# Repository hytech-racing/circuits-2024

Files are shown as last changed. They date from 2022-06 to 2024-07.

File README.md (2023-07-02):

HyTech Logo

# 2024 Circuits

Repository for all of the circuits for the 2023-2024 car.

## Getting Started with this Git Repository
1. Follow HyTech's [Software Guide](https://github.com/hytech-racing/training/tree/master/Resources).
2. Create a GitHub account if you don't already have one.
3. Download and install [GitHub Desktop](https://desktop.github.com/) (basic) or [Git CLI](https://git-scm.com/book/en/v2/Getting-Started-Installing-Git) (advanced).
    * If you are using GitHub Desktop for the first time, be sure to read the [User Guide](https://help.github.com/desktop/guides/).
    * If you are using Git for the first time, you should start off by reading a tutorial. There are many available online:
        * [Pro Git book](https://git-scm.com/book/en/v2)
        * [Atlassian Git Tutorial](https://www.atlassian.com/git/tutorials/)
    * You may want to keep a copy of [GitHub's Git Cheat Sheet](https://services.github.com/kit/downloads/github-git-cheat-sheet.pdf) as a reference.
4. Talk to your subteam lead to be added to the team within the GitHub organization.
5. Clone this repository to your computer using the URLs:
    * SSH: `git@github.com:hytech-racing/circuits-2024.git`
    * HTTPS: `https://github.com/hytech-racing/circuits-2024.git`

## Getting Started with EAGLE
1. Follow HyTech's [Software Guide](https://github.com/hytech-racing/training/tree/master/Resources).
2. Download and install [EAGLE](https://www.autodesk.com/products/eagle/overview)
3. Get the free [Educational License](https://www.autodesk.com/education/free-software/eagle) (a .edu email address is required)

## Github Software Guidelines and Electrical Designs Rules Review Process
Follow HyTech's [Github Software Guidelines](https://gtvault.sharepoint.com/:w:/r/sites/HyTechRacing2/Shared%20Documents/Electrical%20-%20All/HT06/Guidelines%20Rules%20and%20Procedures/Github%20Software%20Guide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) to understand our development flow and pull request procedure.
Follow HyTech's [Electrical Designs Rules Review Process](https://gtvault.sharepoint.com/:w:/r/sites/HyTechRacing2/Shared%20Documents/Electrical%20-%20All/HT06/Guidelines%20Rules%20and%20Procedures/Electrical%20Designs%20Ru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) to understand circuit design flow. 

## Circuit Board Versioning Scheme
* New boards must start their numbering at revision 1.
* Revision numbers must be incremented by 1 when a physical board is manufactured, but not at any other time.
* After a board is manufactured, the files corresponding to the manufactured version should not be modified.
* Circuit boards based off of a previous year's design should increment based off of the previous board's revision number.

## More Information
* [Software Guide](https://github.com/hytech-racing/training/tree/master/Resources)
* [Team Site](https://hytechracing.gatech.edu/)
* [Facebook](https://www.facebook.com/HyTechRacing/)
* [Engage](https://gatech.campuslabs.com/engage/organization/hytech-racing)

## License
This project is licensed under the GPL License v3.0. See the [LICENSE](LICENSE) file for more information.

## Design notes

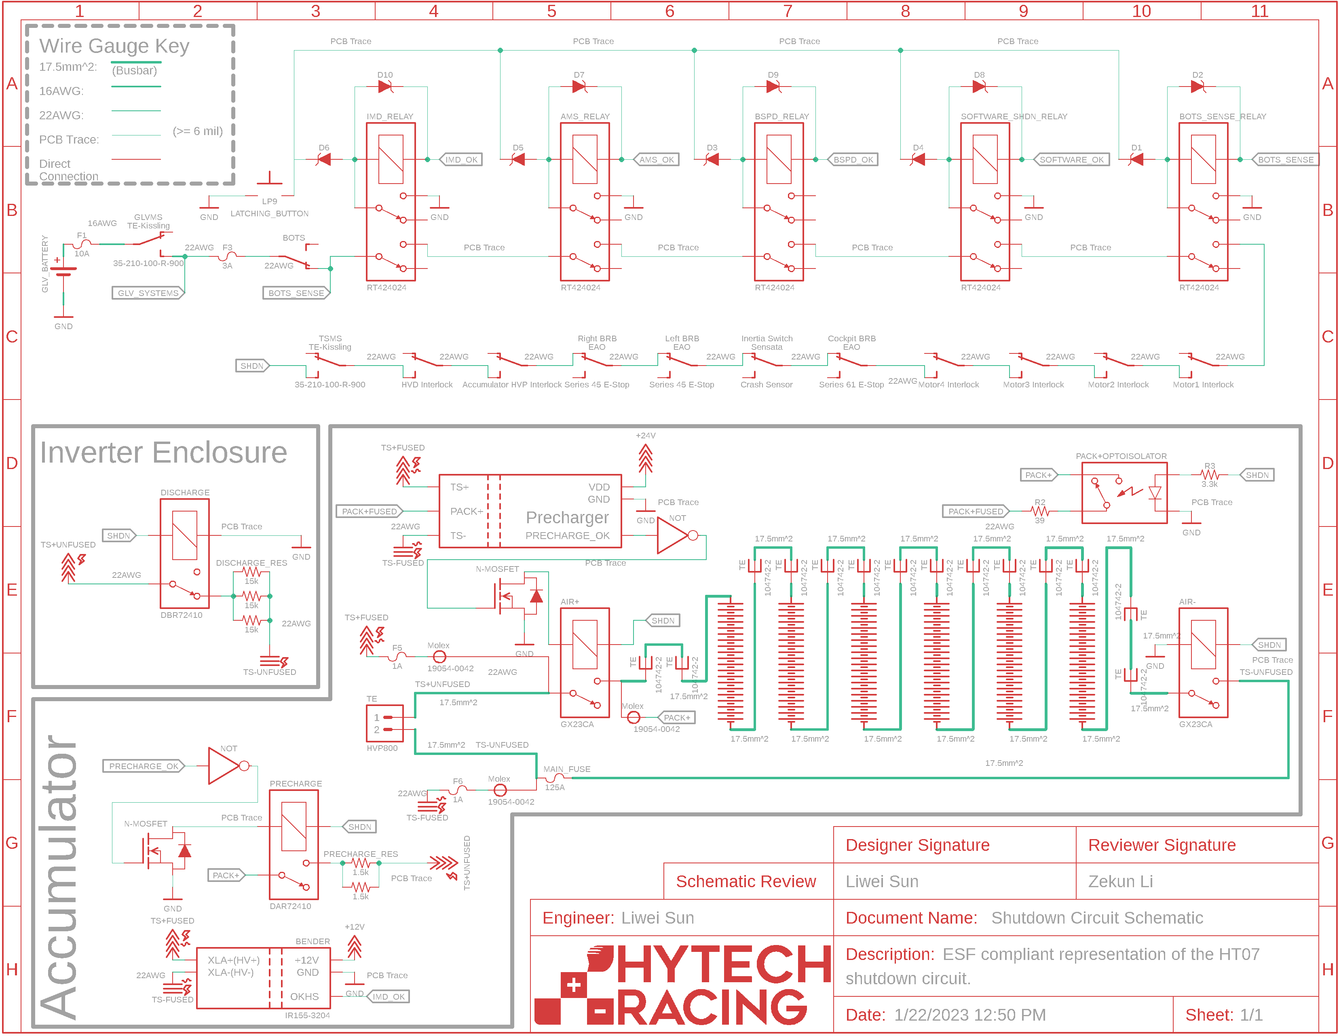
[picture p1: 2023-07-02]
ESF Schematics/2023/Shutdown Circuit Schematic.png

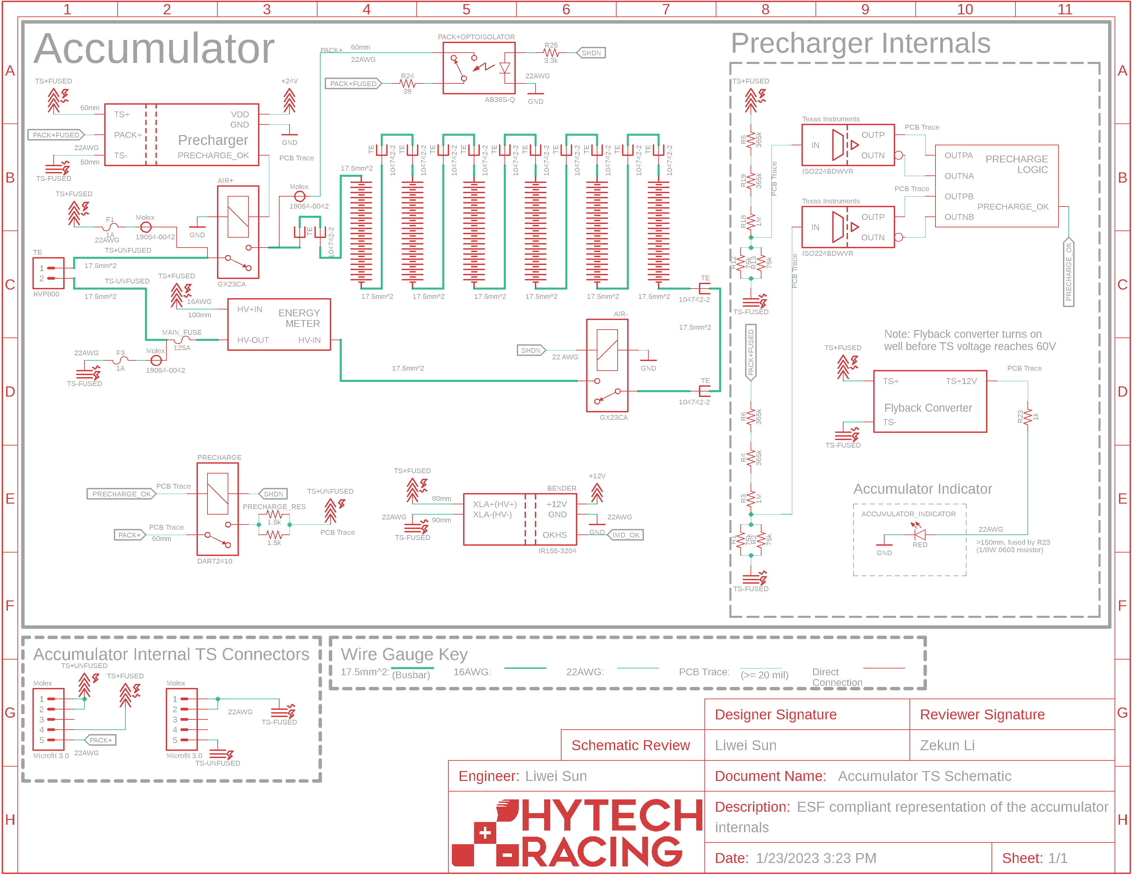
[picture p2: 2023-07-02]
ESF Schematics/2023/Accumulator TS Schematic.png

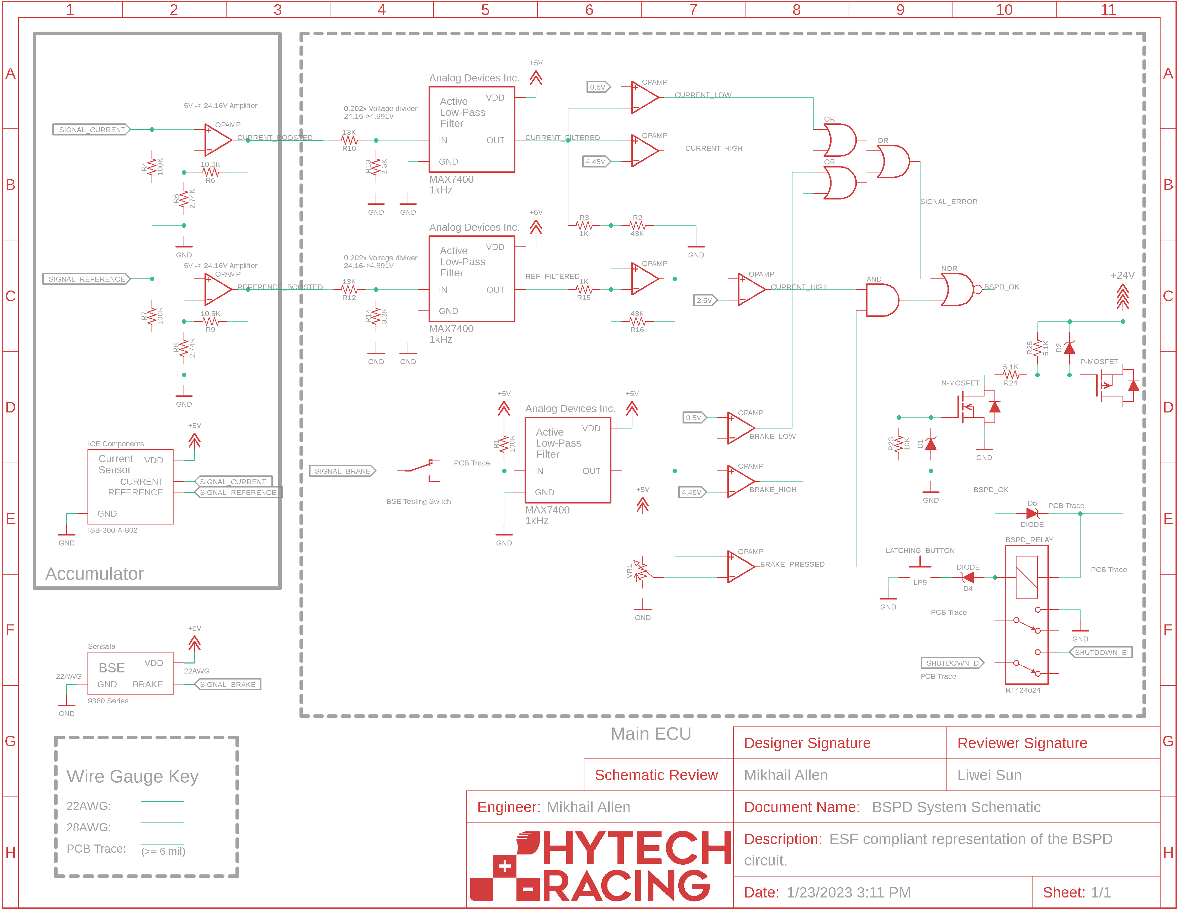
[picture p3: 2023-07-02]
ESF Schematics/2023/BSPD System Schematic.png

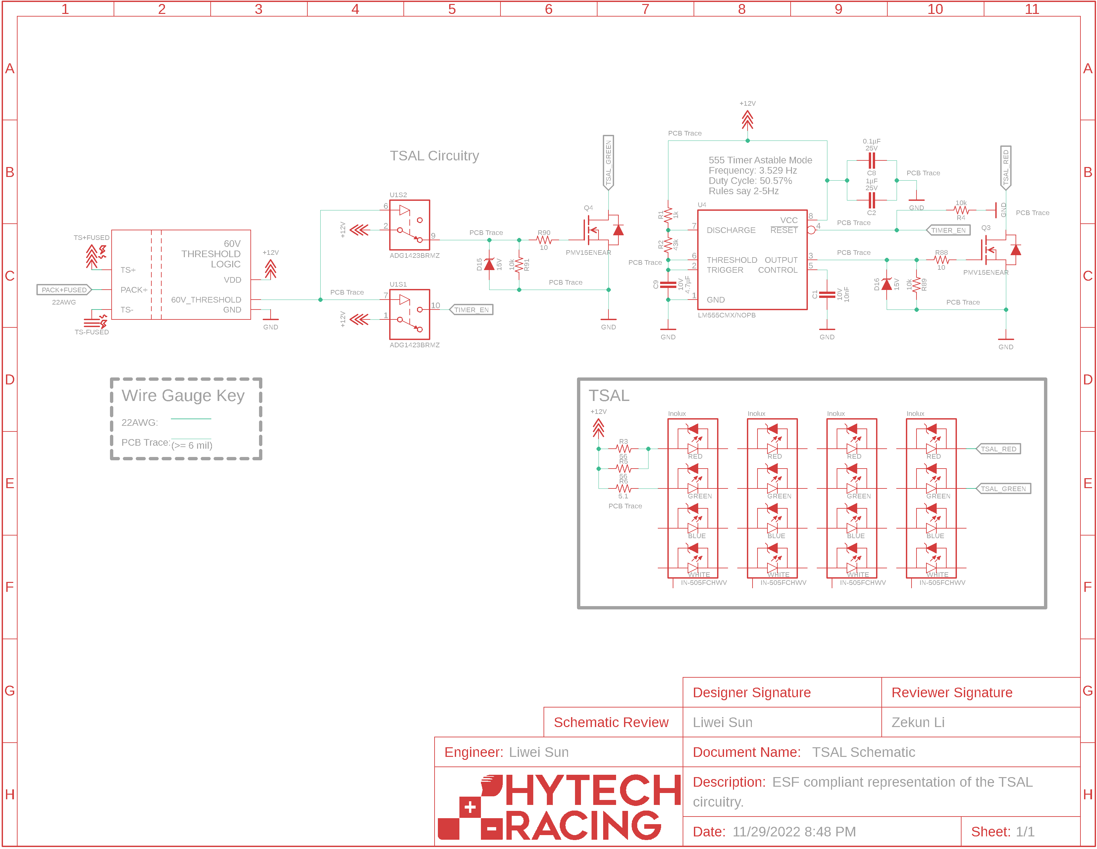
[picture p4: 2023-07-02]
ESF Schematics/2023/TSAL Schematic.png

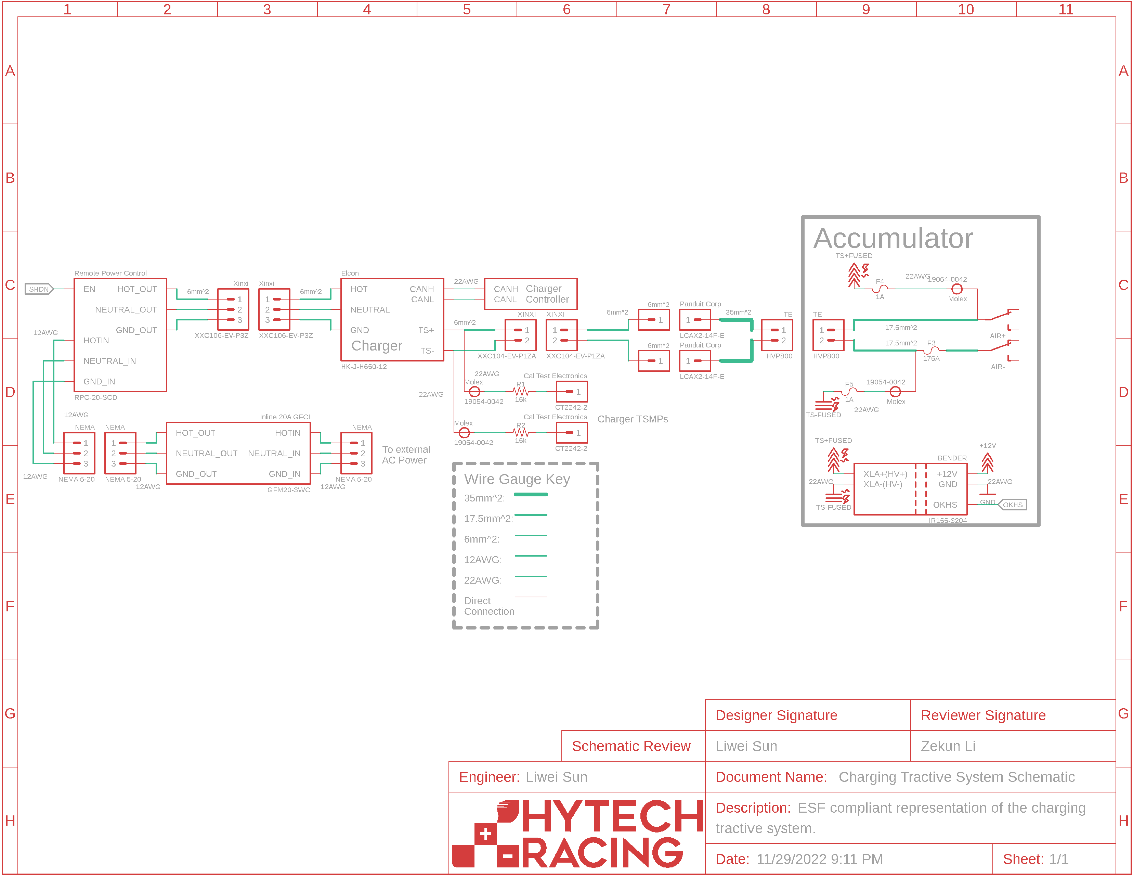
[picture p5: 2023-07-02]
ESF Schematics/2023/Charging Tractive System Schematic.png

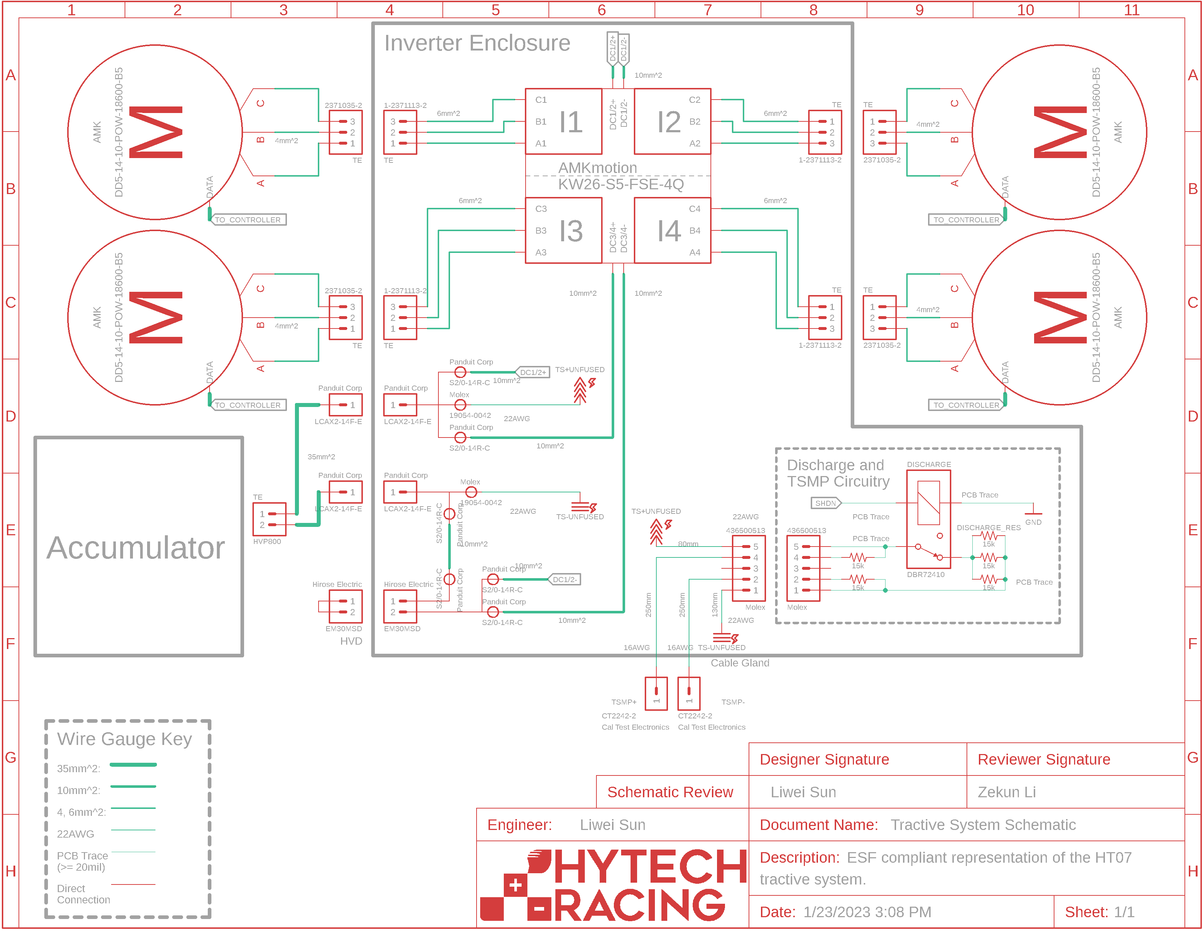
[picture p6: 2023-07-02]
ESF Schematics/2023/Tractive System Schematic.png

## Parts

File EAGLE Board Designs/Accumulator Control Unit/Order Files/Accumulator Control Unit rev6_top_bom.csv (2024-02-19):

Comment | Designator | Footprint | LCSC Part #
ADG1423 | U27 | MSOP-10
ADM8316WBX30 | U21 | SOT-23-5
CAPACITOR_0603_10V_0.1UF | C10 C11 C14 C15 C19 C20 C22 C23 C24 C25 C30 C33 C37 C38 C39 C40 C41 C42 C53 C61 | 0603-CAP
CAPACITOR_0603_10V_1UF | C6 C9 C18 C32 C34 C63 C64 | 0603-CAP
CAPACITOR_0603_10V_4.7NF | C12 C21 | 0603-CAP
CAPACITOR_0603_10V_4.7UF | C5 C28 | 0603-CAP
CAPACITOR_0603_10V_10NF | C7 C13 C17 C52 C54 | 0603-CAP
CAPACITOR_0603_10V_68NF | C56 C57 | 0603-CAP
CAPACITOR_0603_16V_0.47UF | C31 C36 C62 C65 | 0603-CAP
CAPACITOR_0603_25V_0.1UF | C26 C29 | 0603-CAP
CAPACITOR_0603_25V_1UF | C27 C43 C55 | 0603-CAP
CAPACITOR_0603_25V_10UF | C4 | 0603-CAP
CAPACITOR_0603_50V_0.1UF | C8 C16 | 0603-CAP
CAPACITOR_0805_50V_10UF | C1 C2 C3 | 0805-CAP
FUSE_0603_.75A | F1 F2 | 0603-FUSE
LED_0603_BLUE | 5V WATCHDOG | 0603-LED
LED_0603_GREEN | 3.3V AMS_OK TSAL_GREEN | 0603-LED
LED_0603_ORANGE | 24V IMD_OK | 0603-LED
LED_0603_RED | 12V PRECHARGE_OK TEENSY_OK TSAL_RED | 0603-LED
LED_0603_YELLOW | OKHS | 0603-LED
LM555 | U15 | SOIC-08(NARROW 0.15")
LOGICGATE_AND_DCK3 | U23 U24 U25 | SC-70-5
LOGICGATE_BUFFER | U20 | SC-70-5
LTC6820 | U7 U32 | MSOP-16
OPAMP_1_CHANNEL_OPA991 | U4 U5 U8 U9 U11 U12 U13 U16 U18 U22 U26 U33 | SC-70-5
OPAMP_2_CHANNEL_OPA_2991 | U17 U19 | SOT-23-8
RELAY_SOLIDSTATE_NO_DIP-4 | K1 U2 U3 | DIP-4
RESISTOR_0603_ | R13 R15 | 0603-RES
RESISTOR_0603_1.65K | R30 R103 | 0603-RES
RESISTOR_0603_1K | R24 R45 R65 R73 R83 R96 R102 | 0603-RES
RESISTOR_0603_1K | R89 R97 | 0603-RES
RESISTOR_0603_1M | R92 | 0603-RES
RESISTOR_0603_2.2K | R17 R19 | 0603-RES
RESISTOR_0603_2.74K | R42 R44 | 0603-RES
RESISTOR_0603_2K | R18 R25 R28 R29 R48 R72 R74 R95 | 0603-RES
RESISTOR_0603_3.3K | R49 | 0603-RES
RESISTOR_0603_4.12K | R111 | 0603-RES
RESISTOR_0603_4.64K | R8 R10 R12 | 0603-RES
RESISTOR_0603_5.1K | R4 R16 R21 R110 | 0603-RES
RESISTOR_0603_5.9K | R53 | 0603-RES
RESISTOR_0603_7.5K | R123 R124 R129 R130 | 0603-RES
RESISTOR_0603_8.66K | R93 | 0603-RES
RESISTOR_0603_10 | R1 R6 R70 R71 | 0603-RES
RESISTOR_0603_10.5K | R22 R23 | 0603-RES
RESISTOR_0603_10K | R2 R5 R46 R47 R55 R56 R57 R61 R62 R66 R67 R69 R75 R77 R79 R81 R86 R87 R88 R91 R94 R101 | 0603-RES
RESISTOR_0603_10K | R106 R107 R108 R109 | 0603-RES
RESISTOR_0603_11.5K | R54 | 0603-RES
RESISTOR_0603_12K | R76 R78 R122 R125 R126 R128 R131 R132 | 0603-RES
RESISTOR_0603_14K | R63 R84 | 0603-RES
RESISTOR_0603_18.7K | R14 | 0603-RES
RESISTOR_0603_18.7K_LT | R33 R34 R37 R38 | 0603-RES
RESISTOR_0603_20K | R3 R20 R127 R133 | 0603-RES
RESISTOR_0603_36.5K | R7 R9 R11 R58 | 0603-RES
RESISTOR_0603_43K | R68 | 0603-RES
RESISTOR_0603_43K_LT | R35 R36 R39 R40 | 0603-RES
RESISTOR_0603_60.4 | R26 R27 R50 R51 | 0603-RES
RESISTOR_0603_73.2K | R90 | 0603-RES
RESISTOR_0603_100K | R43 | 0603-RES
RESISTOR_0603_120 | R32 R105 | 0603-RES
RESISTOR_0603_330K | R59 | 0603-RES
RESISTOR_0603_470 | R31 R80 R82 R104 R135 | 0603-RES
RESISTOR_0603_DNP | R41 R52 R60 R64 R85 | 0603-RES
TCAN1051HQV-Q1 | U6 | SOIC-08(NARROW 0.15")
TCAN1051HQV-Q1 | U10 | SOIC-08(NARROW 0.15")
TEST_POINT | BSPD_CURRENT CURRENT_REF CURRENT_SENSE | MICRO_MINIATURE
TEST_POINT | CUR_SHUNT | 5015
TEST_POINT | PACK+_OUT_TEST PC_OK TD+ TD+2 TD- TD-2 | MICRO_MINIATURE
TEST_POINT | TP_3.3V TP_5V TP_12V TP_24V | 5015
TEST_POINT | TP_AMS_OK | MICRO_MINIATURE
TEST_POINT | TP_GND | 5015
TEST_POINT | TP_IMD_OK TP_TSAL_GREEN TP_TSAL_RED TS+_OUT_TEST WATCHDOG_INPUT | MICRO_MINIATURE
TRANSFORMER_HM2112ZNLT_AIRGAP | T1 | HM2112ZNLT_AIRGAP
TRANSISTOR_N_MOS__PMV15ENEA | Q1 Q2 Q3 Q4 | SOT-23
TRANSISTOR_P_MOS_SOT-23_DMP3056L-7 | Q5 | SOT-23
TVS_DO-214AA_28V | D4 D5 D6 D8 | DO-214AA
TVS_DO-214AA_30V | D2 | DO-214AA
TVS__8V | D1 D3 D7 | SOT-23
TVS__15V | D9 D10 | SOT-23
VOLTAGE_REGULATOR_SOT-223_3.3V | U1 | SOT-223
ZENER_1.5SMBJ_12V | D11 | 1.5SMBJ

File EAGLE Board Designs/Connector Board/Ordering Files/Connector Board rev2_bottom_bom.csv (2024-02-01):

Comment | Designator | Footprint | LCSC Part #
RESISTOR_0603_5.1K | R6 R7 R9 R10 | 0603-RES
RESISTOR_0603_10K | R5 R8 R11 R12 | 0603-RES
TRANSISTOR_N_MOS__DMG3406L-7 | Q1 Q3 Q5 | SOT-23
TRANSISTOR_P_MOS_SOT-23_DMP3056L-7 | Q2 Q4 Q6 | SOT-23
TVS__15V | D1 D2 D3 D4 D5 D6 | SOT-23

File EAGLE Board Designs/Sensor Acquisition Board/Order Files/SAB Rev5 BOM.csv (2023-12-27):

Board Quantity | Ordering Quantity | Value | Reference | ATTRITION | CAPACITANCE | COLOR | DKPN | FUSE_TYPE | MANUFACTURER | MOPN | MPN | POWER | RESISTANCE | TEENSY | TOLERANCE | VOLTAGE | VOLTAGE_CONTINUOUS | VOLTAGE_MAX
2 | 4 | 78613/3C_78613/3C | T1, T2 | 100 |  |  | 811-3726-ND |  | Murata Power Solutions | 580-786133C | 78613/3C
6 | 16 | CAPACITOR_0603_10V_0.1UF | C54, C55, C63, C65, C66, C67 | 167 | 0.1µF |  | 720-1688-1-ND |  | Vishay Vitramon | 77-VJ0603Y104JXQPBC | VJ0603Y104JXQPW1BC |  |  |  | 5% | 10V
2 | 12 | CAPACITOR_0603_10V_15PF | C58, C59 | 500 | 15pF |  | 720-VJ0603A150FXQPW1BCCT-ND |  | Vishay Vitramon | 77-VJ0603A150FXQPBC | VJ0603A150FXQPW1BC |  |  |  | 1% | 10V
12 | 22 | CAPACITOR_0603_10V_1UF | C8, C9, C10, C11, C12, C13, C14, C15, C56, C57, C68, C69 | 83 | 1µF |  | 311-1796-1-ND |  | Yageo | 603-CC603KRX7R6BB105 | CC0603KRX7R6BB105 |  |  |  | 10% | 10V
1 | 11 | CAPACITOR_0603_10V_4.7NF | C60 | 1000 | 4.7nF |  | 732-7931-1-ND |  | Würth Elektronik | 710-885012206012 | 885012206012 |  |  |  | 10% | 10V
1 | 11 | CAPACITOR_0603_10V_4.7UF | C61 | 1000 | 4.7µF |  | 1276-1044-1-ND |  | Samsung Electro-Mechanics | 187-CL10A475KP8NNNC | CL10A475KP8NNNC |  |  |  | 10% | 10V
3 | 13 | CAPACITOR_0603_25V_10UF | C3, C5, C6 | 333 | 10µF |  | 490-7202-1-ND |  | Murata Electronics | 81-GRM188R61E106MA3D | GRM188R61E106MA73D |  |  |  | 20% | 25V
6 | 16 | CAPACITOR_0603_35V_0.1UF | C48, C49, C50, C51, C52, C62 | 167 | 0.1µF |  | 587-3354-1-ND |  | Taiyo Yuden | 963-GMK107B7104KAHT | GMK107B7104KAHT |  |  |  | 10% | 35V
2 | 12 | CAPACITOR_0603_35V_1UF | C53, C64 | 500 | 1µF |  | 445-173625-1-ND |  | TDK Corporation | 810-C1608X7R1V105KAE | C1608X7R1V105K080AE |  |  |  | 10% | 35V
3 | 13 | CAPACITOR_0805_50V_10UF | C1, C2, C4 | 333 | 10uF |  | 490-18663-2-ND |  | Murata | 81-GRM21BR61H106KE3L | GRM21BR61H106KE43L |  |  |  | 10% | 50V
1 | 3 | CAPACITOR_ELECTROLYTIC_EEH_AZS_470UF | C7 | 200 | 470uF |  | 10-EEH-AZS1V471BCT-ND |  | Panasonic Electronic Components | 667-EEH-AZS1V471B | EEH-AZS1V471B |  |  |  | 20& | 35V
1 | 3 | CONNECTOR-10_MF_T_V_ | J10 | 200 |  |  | WM1799-ND |  | MOLEX | 538-43045-1014 | 430451014
1 | 3 | CONNECTOR-2_MICROFIT_SMD_RIGHTANGLE_02_SINGLE_BLACK | J11 | 200 |  |  | WM14310CT-ND |  | Molex | 538-43650-0214 | 0436500214
1 | 3 | CONNECTOR-2_μF_T_V_BLACK | J8 | 200 |  |  | WM12762-ND |  | Molex | 538-43650-0217 | 436500217
3 | 5 | CONNECTOR-4_μF_S_RA_ | J4, J5, J9 | 67 |  |  | WM1832CT-ND |  | Molex | 538-0430450411 | 0430450411
5 | 7 | CONNECTOR-4_μF_T_V_BLACK | J2, J3, J7, J13, J15 | 40 |  |  | 2266-43045-0414-ND |  | Molex | 538-43045-0414 | 430450414
1 | 3 | CONNECTOR-6_μF_T_V_BLACK | J12 | 200 |  |  | WM1797-ND |  | Molex | 538-43045-0614 | 430450614
4 | 6 | CONNECTOR-8_μF_T_V_BLACK | J1, J6, J14, J16 | 50 |  |  | WM1798-ND |  | Molex | 538-43045-0814 | 430450814
1 | 3 | FUSE_HOLDER_MINIBLADESMD | XF1 | 200 |  |  | 36-3588-ND | MINI 297 | Keystone Electronics | 534-3588 | 3588
6 | 16 | JUMPER_0603_ | JP4, JP5, JP5V, JP6, JP12V, JP24V | 167 |  |  | 13-RC0603FR-130RLTR-ND |  | YAGEO | 603-RC0603FR-130RL | RC0603FR-130RL
1 | 11 | LED_0603_GREEN | D3 | 1000 |  | Green | 754-1790-1-ND |  | Kingbright | 604-APT1608ZGCK | APT1608ZGCK
1 | 11 | LED_0603_RED | D1 | 1000 |  | Red | 754-1786-1-ND |  | Kingbright | 604-APT1608SECKJ3PRV | APT1608SECK/J3-PRV
1 | 11 | LED_0603_YELLOW | D2 | 1000 |  | Yellow | 754-1788-1-ND |  | Kingbright | 604-APT1608SYCK/J3-PRV | APT1608SYCK/J3-PRV
2 | 4 | LTC6820 | U11, U12 | 100 |  |  |  |  | Analog Devices |  | LTC6820IMS#PBF
1 | 3 | MAX3075 | U14 | 200 |  |  | MAX3075EESA+-ND |  | Analog Devices Inc. | 700-MAX3075EESA | MAX3075EESA+
1 | 3 | MAX3227 | U10 | 200 |  |  | 175-MAX3227EEAE/V+TCT-ND |  | Analog Devices Inc. | 700-MAX3227EAE | MAX3227EEAE/V+T
1 | 3 | MCP3208 | U15 | 200 |  |  | MCP3208T-BI/SLCT-ND |  | Microchip Technology | 579-MCP3208T-BI/SL | MCP3208T-BI/SL
2 | 12 | RESISTOR_0603_1.13K | R15, R17 | 500 |  |  | P1.13KHCT-ND |  | Panasonic Electronic Components | 667-ERJ-3EKF1131V | ERJ-3EKF1131V | 0.1W | 1.13k |  | 1% |  | 75V | 150V
2 | 12 | RESISTOR_0603_1.33K | R14, R16 | 500 |  |  | P1.33KDBCT-ND |  | Panasonic Electronic Components | 667-ERA-3AEB1331V | ERA-3AEB1331V | 0.1W | 1.33k |  | 0.1% |  | 11.53V | 75V
4 | 14 | RESISTOR_0603_120 | R3, R18, R19, R20 | 250 |  |  | P120DBCT-ND |  | Panasonic Electronic Components | 667-ERA-3AEB121V | ERA-3AEB121V | 0.1W | 120 |  | 0.1% |  | 3.46V | 75V
1 | 11 | RESISTOR_0603_1K | R1 | 1000 |  |  | 1712-CPF-A-0603B1K0ETR-ND |  | TE Connectivity Passive Product | 279-CPF-A-0603B1K0E | CPF-A-0603B1K0E | 0.0625W | 1k |  | 0.1% |  | 7.9V | 50V
1 | 11 | RESISTOR_0603_240 | R2 | 1000 |  |  | 311-240HRCT-ND |  | Yageo | 603-RC0603FR-07240RL | RC0603FR-07240RL | 0.1W | 240 |  | 1% |  | 4.90V | 75V
2 | 12 | RESISTOR_0603_2K | R12, R13 | 500 |  |  | 10-ERJ-UP3F2001VTR-ND |  | Panasonic Electronic Components | 667-ERJ-UP3F2001V | ERJ-UP3F2001V | 0.25W | 2k |  | 1% |  | 22.36V | 150V
2 | 12 | RESISTOR_0603_60.4 | R21, R22 | 500 |  |  | 311-60.4HRCT-ND |  | Yageo | 603-RC0603FR-0760R4L | RC0603FR-0760R4L | 0.1W | 60.4 |  | 1% |  | 2.48V | 75V
8 | 18 | RESISTOR_0603_8.35K | R4, R5, R6, R7, R8, R9, R10, R11 | 125 |  |  | 764-1461-2-ND |  | Vishay Dale Thin Film | 71-PTN0603E8351BST1 | PTN0603E8351BST1 | 0.15W | 8.35k |  | 0.1% |  | 28.90V | 75V
1 | 3 | TCAN1051HQV-Q1 | U13 | 200 |  |  | 296-49935-1-ND |  | Texas Instruments | 595-TCAN1051HGVDQ1 | TCAN1051HGVDRQ1
1 | 3 | TEENSY_4.0SM | A3 | 200 |  |  |  |  |  |  |  |  |  | 4.0
17 | 19 | TEST_POINT | 3V3, 5V, 12V, CAN_H, CAN_L, CLK, GND, MISO, MOSI, RH_N, RH_P, RL_IM, RL_IP, RR_IM, RR_IP, RXD, TXD | 12 |  |  | 36-5015CT-ND |  | Keystone Electronics | 534-5015 | 5015
4 | 6 | TVS_BIDIRECTIONAL_DUAL | D7, D9, D11, D12 | 50 |  |  | 296-25281-1-ND |  | Texas Instruments | 595-TPD2E007DCKR | TPD2E007DCKR
2 | 4 | TVS_BIDIRECTIONAL_DUALRS422 | D8, D10 | 100 |  |  | SM712CT-ND |  | Semtech Corporation | 947-SM712.TCT | SM712.TCT
1 | 3 | TVS_DO-214AA_30V | D6 | 200 |  |  | 118-1.5SMBJ30ATR-ND |  | Bourns Inc. | 652-1.5SMBJ30A | 1.5SMBJ30A |  |  |  |  | 30V
1 | 3 | TVS_DO-219AB_14V | D4 | 200 |  |  | SMF14A-E3-08GITR-ND |  | Vishay General Semiconductor | 78-SMF14A-E3-08 | SMF14A-E3-08 |  |  |  |  | 14V
1 | 3 | VOLTAGE_REGULATOR_MODULE_OKI-78SR_12V | A1 | 200 |  |  | 811-3293-ND |  | Murata Power Solutions Inc. | 580-OKI78SR12/1W36C | OKI-78SR-12/1.0-W36-C
1 | 3 | VOLTAGE_REGULATOR_MODULE_OKI-78SR_5V | A2 | 200 |  |  | 811-2196-5-ND |  | Murata Power Solutions Inc. | 580-OKI78SR5/1.5W36C | OKI-78SR-5/1.5-W36-C
1 | 3 | VOLTAGE_REGULATOR_SOT-223_3.3V | U1 | 200 |  |  | LMS8117AMP-3.3/NOPBCT-ND |  | Texas Instruments | 926-LMS8117AMP33NOPB | LMS8117AMP-3.3/NOPB

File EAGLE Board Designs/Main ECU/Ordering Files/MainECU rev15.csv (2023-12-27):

Board Quantity | Ordering Quantity | Value | Reference | ATTRITION | BATTERY_TYPE | CAPACITANCE | COLOR | CURRENT | DKPN | MANUFACTURER | MOPN | MPN | POWER | RESET_VOLTAGE | RESISTANCE | TEENSY | TIMEOUT | TOLERANCE | VOLTAGE | VOLTAGE_CONTINUOUS | VOLTAGE_MAX
1 | 3 | ADM8316WBX30 | U31 | 200 |  |  |  |  | ADM8316WBX30ARJZR7TR-ND | Analog Devices Inc. | 584-M8316WBX30ARJZR7 | ADM8316WBX30ARJZR7 |  | 3V |  |  | 102ms
1 | 3 | BATTERY_HOLDER_KEYSTONE_498 | XB1 | 200 | 1/3N |  |  |  | 36-498-ND | Keystone Electronics | 534-498 | 498
1 | 3 | BUTTON | S1 | 200 |  |  |  |  | SW415-ND | Omron | 653-B3S-1000 | B3S-1000
30 | 40 | CAPACITOR_0603_10V_0.1UF | C1, C6, C9, C10, C14, C15, C16, C17, C18, C19, C20, C22, C25, C29, C33, C35, C41, C46, C51, C57, C58, C59, C60, C62, C63, C67, C68, C69, C70, C75 | 33 |  | 0.1µF |  |  | 720-1688-1-ND | Vishay Vitramon | 77-VJ0603Y104JXQPBC | VJ0603Y104JXQPW1BC |  |  |  |  |  | 5% | 10V
2 | 12 | CAPACITOR_0603_10V_10NF | C32, C37 | 500 |  | 10nF |  |  | 311-4054-1-ND | Yageo | 603-CC603KRX7R6BB103 | CC0603KRX7R6BB103 |  |  |  |  |  | 10% | 10V
2 | 12 | CAPACITOR_0603_10V_15PF | C21, C23 | 500 |  | 15pF |  |  | 720-VJ0603A150FXQPW1BCCT-ND | Vishay Vitramon | 77-VJ0603A150FXQPBC | VJ0603A150FXQPW1BC |  |  |  |  |  | 1% | 10V
21 | 31 | CAPACITOR_0603_10V_1UF | C2, C11, C13, C26, C30, C34, C39, C40, C44, C45, C49, C50, C52, C56, C64, C73, C74, C78, C79, C82, C83 | 48 |  | 1µF |  |  | 311-1796-1-ND | Yageo | 603-CC603KRX7R6BB105 | CC0603KRX7R6BB105 |  |  |  |  |  | 10% | 10V
2 | 12 | CAPACITOR_0603_10V_4.7NF | C24, C61 | 500 |  | 4.7nF |  |  | 732-7931-1-ND | Würth Elektronik | 710-885012206012 | 885012206012 |  |  |  |  |  | 10% | 10V
12 | 22 | CAPACITOR_0603_16V_0.47UF | C36, C38, C42, C43, C47, C48, C71, C72, C76, C77, C80, C81 | 83 |  | 0.47µF |  |  | 445-5192-1-ND | TDK Corporation | 810-C1608X7R1C474K | C1608X7R1C474K080AC |  |  |  |  |  | 10% | 16V
1 | 11 | CAPACITOR_0603_25V_1.2NF | C31 | 1000 |  | 1.2nF |  |  | 311-4079-2-ND | YAGEO | 603-CC603KRX7R8BB122 | CC0603KRX7R8BB122 |  |  |  |  |  | 10% | 25V
3 | 13 | CAPACITOR_0603_25V_10UF | C4, C5, C28 | 333 |  | 10µF |  |  | 490-7202-1-ND | Murata Electronics | 81-GRM188R61E106MA3D | GRM188R61E106MA73D |  |  |  |  |  | 20% | 25V
2 | 12 | CAPACITOR_0603_50V_1UF | C7, C8 | 500 |  | 1uF |  |  | 587-2400-2-ND | Taiyo Yuden | 963-UMK107BJ105KA-T | UMK107BJ105KA-T |  |  |  |  |  | 10% | 50V
1 | 11 | CAPACITOR_0805_50V_10UF | C27 | 1000 |  | 10uF |  |  | 490-18663-2-ND | Murata | 81-GRM21BR61H106KE3L | GRM21BR61H106KE43L |  |  |  |  |  | 10% | 50V
1 | 3 | CAPACITOR_ELECTROLYTIC_EEH_AZS_470UF | C3 | 200 |  | 470uF |  |  | 10-EEH-AZS1V471BCT-ND | Panasonic Electronic Components | 667-EEH-AZS1V471B | EEH-AZS1V471B |  |  |  |  |  | 20& | 35V
2 | 4 | CONNECTOR-24_CONNECTOR-24_ | J1, J2 | 100 |  |  |  |  | EHT-112-01-F-D-ND | Samtec | 200-EHT11201FD | EHT-112-01-F-D
2 | 4 | DNP | JP9, JP11 | 100 |  |  |  |  | 13-RC0603FR-130RLTR-ND | YAGEO | 603-RC0603FR-130RL | RC0603FR-130RL
4 | 14 | JUMPER_0603_ | JP2, JP4, JP10, JP12 | 250 |  |  |  |  | 13-RC0603FR-130RLTR-ND | YAGEO | 603-RC0603FR-130RL | RC0603FR-130RL
2 | 4 | JUMPER__1X02 | JP1, JP3 | 100 |  |  |  |  | S1011EC-02-ND | Sullins Connector Solutions |  | PRPC002SAAN-RC
1 | 2 | LED_0603_GREEN | F | 100 |  |  | Green |  | 754-1790-1-ND | Kingbright | 604-APT1608ZGCK | APT1608ZGCK
6 | 16 | LED_0603_GREEN | B, BSPD, C, D, E, G | 167 |  |  | Green |  | 754-1790-1-ND | Kingbright | 604-APT1608ZGCK | APT1608ZGCK
4 | 14 | LED_0603_ORANGE | BMS, IMD, SWOK, WDOG | 250 |  |  | Orange |  | 754-1120-1-ND | Kingbright | 604-APT1608SECK | APT1608SECK
9 | 19 | LED_0603_RED | B_HI, B_MIS, C_HI, C_MIS, ESP, GPS, LTE, MQTT, RTK | 111 |  |  | Red |  | 754-1786-1-ND | Kingbright | 604-APT1608SECKJ3PRV | APT1608SECK/J3-PRV
1 | 11 | LED_0603_WHITE | LATCH | 1000 |  |  | White |  | SM0603UWC-ND | Bivar Inc. | 749-SM0603UWC | SM0603UWC
2 | 12 | LED_0603_YELLOW | 3V3, 5V0 | 500 |  |  | Yellow |  | 754-1788-1-ND | Kingbright | 604-APT1608SYCK/J3-PRV | APT1608SYCK/J3-PRV
1 | 3 | LOGICGATE_AND_DCK3 | U15 | 200 |  |  |  |  | 296-SN74LVC1G08DCK3TR-ND | Texas Instruments | 595-SN74LVC1G08DCK3 | SN74LVC1G08DCK3
1 | 3 | LOGICGATE_NOR | U13 | 200 |  |  |  |  | 296-11598-1-ND | Texas Instruments | 595-SN74LVC1G02DCKR | SN74LVC1G02DCKR
5 | 7 | LOGICGATE_OR | U8, U9, U10, U11, U12 | 40 |  |  |  |  | 296-22348-2-ND | Texas Instruments | 595-SN74LVC32IDCKREP | SN74LVC1G32IDCKREP
2 | 4 | LTC6820 | U2, U3 | 100 |  |  |  |  |  | Analog Devices |  | LTC6820IMS#PBF
1 | 3 | MAX3074EESA+ | U16 | 200 |  |  |  |  | MAX3074EESA+-ND | Maxim Integrated | 700-MAX3074EESA | MAX3074EESA+
2 | 4 | MAX7400 | U17, U18 | 100 |  |  |  |  | MAX7400CSA+-ND | Maxim Integrated | 700-MAX7400CSA | MAX7400CSA+
1 | 3 | MCP3208 | U6 | 200 |  |  |  |  | MCP3208T-BI/SLCT-ND | Microchip Technology | 579-MCP3208T-BI/SL | MCP3208T-BI/SL
1 | 3 | NRF9160LTE | A4 | 200 |  |  |  |  | 1568-WRL-17354-ND | SparkFun Electronics | 474-WRL-17354 | WRL-17354
1 | 3 | OPAMP_1_CHANNEL_OPA991 | U7 | 200 |  |  |  |  | 296-OPA991IDCKRCT-ND | Texas Instruments | 595-OPA991IDCKR | OPA991IDCKR
10 | 12 | OPAMP_2_CHANNEL_OPA_2991 | U19, U20, U21, U22, U23, U24, U25, U26, U27, U32 | 20 |  |  |  |  | 296-OPA2991IDDFRCT-ND | Texas Instruments | 595-OPA2991IDDFR | OPA2991IDDFR
5 | 7 | RELAY_DPDT_07DSMT | K1, K2, K3, K4, K5 | 40 |  |  |  |  | PB2077CT-ND | TE Connectivity | 655-3-1462039-7 | 3-1462039-7
4 | 14 | RESISTOR_0603_1.13K | R63, R64, R151, R153 | 250 |  |  |  |  | P1.13KHCT-ND | Panasonic Electronic Components | 667-ERJ-3EKF1131V | ERJ-3EKF1131V | 0.1W |  | 1.13k |  |  | 1% |  | 75V | 150V
1 | 11 | RESISTOR_0603_1.24K | R65 | 1000 |  |  |  |  | 311-1.24KHRCT-ND | Yageo | 603-RC0603FR-071K24L | RC0603FR-071K24L | 0.1W |  | 1.24k |  |  | 1% |  | 11.14V | 75V
2 | 12 | RESISTOR_0603_1.33K | R150, R152 | 500 |  |  |  |  | P1.33KDBCT-ND | Panasonic Electronic Components | 667-ERA-3AEB1331V | ERA-3AEB1331V | 0.1W |  | 1.33k |  |  | 0.1% |  | 11.53V | 75V
3 | 13 | RESISTOR_0603_10.2K | R33, R34, R62 | 333 |  |  |  |  | P10.2KDBCT-ND | Panasonic Electronic Components | 667-ERA-3AEB1022V | ERA-3AEB1022V | 0.1W |  | 10.2k |  |  | 0.1% |  | 31.94V | 75V
18 | 28 | RESISTOR_0603_10K | R1, R3, R54, R67, R69, R73, R74, R88, R95, R102, R109, R116, R122, R133, R134, R143, R147, R149 | 56 |  |  |  |  | P10KBDCT-ND | Panasonic Electronic Components | 667-ERA-3ARB103V | ERA-3ARB103V | 0.1W |  | 10k |  |  | 0.1% |  | 31.62V | 75V
4 | 14 | RESISTOR_0603_120 | R23, R30, R55, R56 | 250 |  |  |  |  | P120DBCT-ND | Panasonic Electronic Components | 667-ERA-3AEB121V | ERA-3AEB121V | 0.1W |  | 120 |  |  | 0.1% |  | 3.46V | 75V
12 | 22 | RESISTOR_0603_12K | R82, R83, R84, R90, R91, R97, R98, R104, R105, R111, R112, R118 | 83 |  |  |  |  | 311-12.0KHRCT-ND | Yageo | 603-RC0603FR-0712KL | RC0603FR-0712KL | 0.1W |  | 12k |  |  | 1% |  | 34.64V | 75V
1 | 11 | RESISTOR_0603_14K | R53 | 1000 |  |  |  |  | RT0603BRB0714KL-ND | YAGEO | 603-RT0603BRB0714KL | RT0603BRB0714KL | 0.1W |  | 14k |  |  | 0.1% |  | 37.4V | 75V
6 | 16 | RESISTOR_0603_15K | R89, R96, R103, R110, R117, R123 | 167 |  |  |  |  | P15KBDCT-ND | Panasonic Electronic Components | 667-ERA-3ARB153V | ERA-3ARB153V | 0.1W |  | 15k |  |  | 0.1% |  | 38.73V | 75V
2 | 12 | RESISTOR_0603_18.7K | R71, R72 | 500 |  |  |  |  | 311-18.7KHRCT-ND | Yageo | 603-RC0603FR-0718K7L | RC0603FR-0718K7L | 0.1W |  | 18.7k |  |  | 1% |  | 43.24V | 75V
1 | 11 | RESISTOR_0603_180 | R28 | 1000 |  |  |  |  | 311-180HRCT-ND | Yageo | 603-RC0603FR-07180RL | RC0603FR-07180RL | 0.1W |  | 180 |  |  | 1% |  | 4.24V | 75V
2 | 12 | RESISTOR_0603_1K | R46, R50 | 500 |  |  |  |  | 1712-CPF-A-0603B1K0ETR-ND | TE Connectivity Passive Product | 279-CPF-A-0603B1K0E | CPF-A-0603B1K0E | 0.0625W |  | 1k |  |  | 0.1% |  | 7.9V | 50V
1 | 11 | RESISTOR_0603_2.18K | R68 | 1000 |  |  |  |  | 13-RT0805BRD072K18LTR-ND | YAGEO | 603-RT0805BRD072K18L | RT0805BRD072K18L | 0.125W |  | 2.18k |  |  | 0.1% |  | 16.51V | 150V
1 | 11 | RESISTOR_0603_2.55K | R66 | 1000 |  |  |  |  | 311-2.55KHRCT-ND | Yageo | 603-RC0603FR-072K55L | RC0603FR-072K55L | 0.1W |  | 2.55k |  |  | 1% |  | 15.97V | 75V
5 | 15 | RESISTOR_0603_240 | R29, R41, R44, R48, R49 | 200 |  |  |  |  | 311-240HRCT-ND | Yageo | 603-RC0603FR-07240RL | RC0603FR-07240RL | 0.1W |  | 240 |  |  | 1% |  | 4.90V | 75V
17 | 27 | RESISTOR_0603_2K | R5, R8, R11, R14, R17, R20, R24, R25, R26, R27, R31, R32, R57, R58, R59, R60, R61 | 59 |  |  |  |  | 10-ERJ-UP3F2001VTR-ND | Panasonic Electronic Components | 667-ERJ-UP3F2001V | ERJ-UP3F2001V | 0.25W |  | 2k |  |  | 1% |  | 22.36V | 150V
2 | 12 | RESISTOR_0603_3.3K | R2, R4 | 500 |  |  |  |  | P20340TR-ND | Panasonic Electronic Components | 667-ERJ-PB3D3301V | ERJ-PB3D3301V | 0.3W |  | 3.3k |  |  | 0.5% |  | 25.69V | 150
6 | 16 | RESISTOR_0603_30K | R87, R94, R101, R108, R115, R121 | 167 |  |  |  |  | P30KBDCT-ND | Panasonic Electronic Components | 667-ERA-3ARB303V | ERA-3ARB303V | 0.1W |  | 30k |  |  | 0.1% |  | 54.77V | 75V
9 | 19 | RESISTOR_0603_36.5K | R7, R10, R13, R16, R19, R22, R138, R139, R140 | 111 |  |  |  |  | 311-36.5KHRCT-ND | Yageo | 603-RC0603FR-0736K5L | RC0603FR-0736K5L | 0.1W |  | 36.5k |  |  | 1% |  | 60.42V | 75V
9 | 19 | RESISTOR_0603_4.64K | R6, R9, R12, R15, R18, R21, R135, R136, R137 | 111 |  |  |  |  | 311-4.64KHRCT-ND | Yageo | 603-RC0603FR-074K64L | RC0603FR-074K64L | 0.1W |  | 4.64k |  |  | 1% |  | 21.54V | 75V
2 | 12 | RESISTOR_0603_43K | R45, R51 | 500 |  |  |  |  | 311-43.0KHRCT-ND | Yageo | 603-RC0603FR-0743KL | RC0603FR-0743KL | 0.1W |  | 43k |  |  | 1% |  | 65.57V | 75V
4 | 14 | RESISTOR_0603_5.1K | R144, R145, R146, R148 | 250 |  |  |  |  | 311-5.10KHRTR-ND | Yageo | 603-RC0603FR-075K1L | RC0603FR-075K1L | 0.1W |  | 5.1k |  |  | 1% |  | 22.58V | 75V
4 | 14 | RESISTOR_0603_60.4 | R47, R52, R141, R142 | 250 |  |  |  |  | 311-60.4HRCT-ND | Yageo | 603-RC0603FR-0760R4L | RC0603FR-0760R4L | 0.1W |  | 60.4 |  |  | 1% |  | 2.48V | 75V
12 | 22 | RESISTOR_0603_7.5K | R85, R86, R92, R93, R99, R100, R106, R107, R113, R114, R119, R120 | 83 |  |  |  |  | P20072CT-ND | Panasonic Electronic Components | 667-ERJ-PB3B7501V | ERJ-PB3B7501V | 0.2W |  | 7.5k |  |  | 0.1% |  | 38.73V | 150V
2 | 12 | RESISTOR_0603_8.35K | R131, R132 | 500 |  |  |  |  | 764-1461-2-ND | Vishay Dale Thin Film | 71-PTN0603E8351BST1 | PTN0603E8351BST1 | 0.15W |  | 8.35k |  |  | 0.1% |  | 28.90V | 75V
1 | 11 | RESISTOR_0603_DNP | R70 | 1000 |  |  |  |  |  |  |  |  |  |  | DNP
2 | 4 | RESISTOR_TRIMPOT_10K_3362P | VR1, VR2 | 100 |  |  |  |  | 3362P-103LF-ND | Bourns Inc. | 652-3362P-1-103LF | 3362P-1-103LF | 0.5W |  | 10k |  |  | 10% | 70.711V
1 | 11 | SCHOTTKY_1206_40V | D2 | 1000 |  |  |  |  | 478-7806-1-ND | KYOCERA AVX | 581-SD1206S040S2R0 | SD1206S040S2R0 |  |  |  |  |  |  | 40 V
10 | 12 | SCHOTTKY_SOD323_30V | D3, D9, D10, D11, D12, D13, D14, D15, D16, D17 | 20 |  |  |  | 0.8A | CUS08F30H3FTR-ND | Toshiba Semiconductor and Storage | 757-CUS08F30H3F | CUS08F30 |  |  |  |  |  |  | 30V
4 | 6 | TCAN1051HQV-Q1 | U4, U14, U29, U30 | 50 |  |  |  |  | 296-49935-1-ND | Texas Instruments | 595-TCAN1051HGVDQ1 | TCAN1051HGVDRQ1
1 | 3 | TEENSY_4.1 | A3 | 200 |  |  |  |  |  |  |  |  |  |  |  | 4.1
1 | 3 | TEENSY_4.1_SMT | A2 | 200 |  |  |  |  |  |  |  |  |  |  |  | 4.1
13 | 15 | TEST_POINT | CUR, TP1, TP2, TP3, TP4, TP6, TP7, TP8, TP9, TP10, TP11, TP12, TP13 | 15 |  |  |  |  | 36-5015CT-ND | Keystone Electronics | 534-5015 | 5015
1 | 3 | TRANSFORMER_HM2112ZNLT | T1 | 200 |  |  |  |  | 1840-1036-1-ND | Pulse Electronics | 673-HM2112ZNLT | HM2112ZNLT
2 | 4 | TRANSISTOR_N_MOS__DMG3406L-7 | Q1, Q4 | 100 |  |  |  |  | DMG3406L-7DITR-ND | Diodes Incorporated | 621-DMG3406L-7 | DMG3406L-7
2 | 7 | TRANSISTOR_P_MOS_SOT-23_DMP3056L-7 | Q2, Q3 | 250 |  |  |  |  | DMP3056L-7DITR-ND | Diodes Incorporated | 621-DMP3056L-7 | DMP3056L-7
2 | 4 | TVS_BIDIRECTIONAL_DUAL | D23, D24 | 100 |  |  |  |  | 296-25281-1-ND | Texas Instruments | 595-TPD2E007DCKR | TPD2E007DCKR
5 | 7 | TVS_DO-214AA_30V | D4, D5, D6, D7, D8 | 40 |  |  |  |  | 118-1.5SMBJ30ATR-ND | Bourns Inc. | 652-1.5SMBJ30A | 1.5SMBJ30A |  |  |  |  |  |  | 30V
4 | 6 | TVS__15V | D19, D20, D21, D22 | 50 |  |  |  |  | GSOT15-E3-08CT-ND | Vishay General Semiconductor - Diodes Division | 78-GSOT15-E3-08 | GSOT15-E3-08 |  |  |  |  |  |  | 15V
1 | 3 | TVS__5V | D18 | 200 |  |  |  |  | GSOT03-E3-08CT-ND | Vishay General Semiconductor - Diodes Division | 78-GSOT03-E3-08 | GSOT03-E3-08 |  |  |  |  |  |  | 3.3V
1 | 3 | VOLTAGE_REGULATOR_MODULE_OKI-78SR_12V | A1 | 200 |  |  |  |  | 811-3293-ND | Murata Power Solutions Inc. | 580-OKI78SR12/1W36C | OKI-78SR-12/1.0-W36-C
1 | 3 | VOLTAGE_REGULATOR_SOT-223_3.3V | U1 | 200 |  |  |  |  | LMS8117AMP-3.3/NOPBCT-ND | Texas Instruments | 926-LMS8117AMP33NOPB | LMS8117AMP-3.3/NOPB

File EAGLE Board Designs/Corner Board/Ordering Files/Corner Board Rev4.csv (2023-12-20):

Board Quantity | Ordering Quantity | Value | Reference | ATTRITION | CAPACITANCE | DKPN | MANUFACTURER | MOPN | MPN | POWER | RESISTANCE | TOLERANCE | VOLTAGE | VOLTAGE_CONTINUOUS | VOLTAGE_MAX
1 | 3 | 78613/3C_78613/3C_AIRGAP | T1 | 200 |  | 811-3726-ND | Murata Power Solutions | 580-786133C | 78613/3C
1 | 3 | BINDER-M12-A_4_PIN | J3 | 200 |  |  | Binder |  | BN86-0531-1120-00004
2 | 12 | CAPACITOR_0603_10V_0.1UF | C18, C19 | 500 | 0.1µF | 720-1688-1-ND | Vishay Vitramon | 77-VJ0603Y104JXQPBC | VJ0603Y104JXQPW1BC |  |  | 5% | 10V
1 | 11 | CAPACITOR_0603_10V_15PF | C20 | 1000 | 15pF | 720-VJ0603A150FXQPW1BCCT-ND | Vishay Vitramon | 77-VJ0603A150FXQPBC | VJ0603A150FXQPW1BC |  |  | 1% | 10V
5 | 15 | CAPACITOR_0603_10V_1UF | C7, C13, C14, C16, C17 | 200 | 1µF | 311-1796-1-ND | Yageo | 603-CC603KRX7R6BB105 | CC0603KRX7R6BB105 |  |  | 10% | 10V
1 | 11 | CAPACITOR_0603_16V_0.47UF | C6 | 1000 | 0.47µF | 445-5192-1-ND | TDK Corporation | 810-C1608X7R1C474K | C1608X7R1C474K080AC |  |  | 10% | 16V
1 | 11 | CAPACITOR_0603_25V_0.1UF | C1 | 1000 | 0.1µF | 1276-1006-1-ND | Samsung Electro-Mechanics | 187-CL10B104KA8NNNC | CL10B104KA8NNNC |  |  | 10% | 25V
1 | 11 | CAPACITOR_0603_25V_1UF | C3 | 1000 | 1µF | 1276-1184-1-ND | Samsung Electro-Mechanics | 187-CL10B105KA8NNNC | CL10B105KA8NNNC |  |  | 10% | 25V
3 | 13 | CAPACITOR_0603_35V_0.1UF | C2, C4, C15 | 333 | 0.1µF | 587-3354-1-ND | Taiyo Yuden | 963-GMK107B7104KAHT | GMK107B7104KAHT |  |  | 10% | 35V
1 | 11 | CAPACITOR_0603_35V_0.47UF | C22 | 1000 | 0.47µF | 445-6928-6-ND | TDK Corporation | 810-CGA3E1X7R1V474K | CGA3E1X7R1V474K080AC |  |  | 10% | 35V
2 | 12 | CAPACITOR_0603_35V_1UF | C5, C21 | 500 | 1µF | 445-173625-1-ND | TDK Corporation | 810-C1608X7R1V105KAE | C1608X7R1V105K080AE |  |  | 10% | 35V
1 | 11 | CAPACITOR_0603_50V_10NF | C11 | 1000 | 10nF | 445-7404-1-ND | TDK Corporation | 810-C1608C0G1H103J | C1608C0G1H103J080AA |  |  | 5% | 50V
2 | 12 | CAPACITOR_0805_50V_10UF | C9, C10 | 500 | 10uF | 490-18663-2-ND | Murata | 81-GRM21BR61H106KE3L | GRM21BR61H106KE43L |  |  | 10% | 50V
1 | 3 | CONNECTOR-2_MICROFIT_SMD_RIGHTANGLE_02_SINGLE_BLACK | J2 | 200 |  | WM14310CT-ND | Molex | 538-43650-0214 | 0436500214
1 | 3 | CONNECTOR-4_μF_S_RA_ | J4 | 200 |  | WM1832CT-ND | Molex | 538-0430450411 | 0430450411
1 | 3 | CONNECTOR-8_AMPHENOL_M12A_08PMMP_ | J1 | 200 |  | 1754-1026-ND | Amphenol LTW | 523-M12A08PMMPSF8001 | M12A-08PMMP-SF8001
1 | 3 | INA823DT | U3 | 200 |  | 296-INA823DTCT-ND | Texas Instruments | 595-INA823DT | INA823DT
4 | 14 | JUMPER_0603_ | JP1, JP2, JP3, JP4 | 250 |  | 13-RC0603FR-130RLTR-ND | YAGEO | 603-RC0603FR-130RL | RC0603FR-130RL
1 | 3 | LTC6820 | U10 | 200 |  |  | Analog Devices |  | LTC6820IMS#PBF
1 | 3 | MCP3204 | U11 | 200 |  | MCP3204-BI/SL-ND | Microchip Technology | 579-MCP3204-BI/SL | MCP3204-BI/SL
2 | 4 | OPAMP_2_CHANNEL_OPA_2991 | U1, U4 | 100 |  | 296-OPA2991IDDFRCT-ND | Texas Instruments | 595-OPA2991IDDFR | OPA2991IDDFR
1 | 2 | RECEPTACLE-2_MICROFIT | O3 | 100 |  | WM1845-ND | Molex | 538-43645-0200 | 0436450200
2 | 4 | RECEPTACLE-4_MICROFIT | O1, O2 | 100 |  | WM11225-ND | Molex | 538-43025-0408 | 0430250408
1 | 11 | RESISTOR_0603_1.13K | R13 | 1000 |  | P1.13KHCT-ND | Panasonic Electronic Components | 667-ERJ-3EKF1131V | ERJ-3EKF1131V | 0.1W | 1.13k | 1% |  | 75V | 150V
1 | 11 | RESISTOR_0603_1.24K | R18 | 1000 |  | 311-1.24KHRCT-ND | Yageo | 603-RC0603FR-071K24L | RC0603FR-071K24L | 0.1W | 1.24k | 1% |  | 11.14V | 75V
1 | 11 | RESISTOR_0603_1.33K | R9 | 1000 |  | P1.33KDBCT-ND | Panasonic Electronic Components | 667-ERA-3AEB1331V | ERA-3AEB1331V | 0.1W | 1.33k | 0.1% |  | 11.53V | 75V
2 | 12 | RESISTOR_0603_1.5M | R5, R17 | 500 |  | 311-1.50MHRCT-ND | Yageo | 603-RC0603FR-071M5L | RC0603FR-071M5L | 0.1W | 1.5M | 1% |  | 75V | 75V
1 | 11 | RESISTOR_0603_10K | R19 | 1000 |  | P10KBDCT-ND | Panasonic Electronic Components | 667-ERA-3ARB103V | ERA-3ARB103V | 0.1W | 10k | 0.1% |  | 31.62V | 75V
1 | 11 | RESISTOR_0603_120 | R10 | 1000 |  | P120DBCT-ND | Panasonic Electronic Components | 667-ERA-3AEB121V | ERA-3AEB121V | 0.1W | 120 | 0.1% |  | 3.46V | 75V
3 | 13 | RESISTOR_0603_12K | R7, R8, R11 | 333 |  | 311-12.0KHRCT-ND | Yageo | 603-RC0603FR-0712KL | RC0603FR-0712KL | 0.1W | 12k | 1% |  | 34.64V | 75V
1 | 11 | RESISTOR_0603_1K | R1 | 1000 |  | 1712-CPF-A-0603B1K0ETR-ND | TE Connectivity Passive Product | 279-CPF-A-0603B1K0E | CPF-A-0603B1K0E | 0.0625W | 1k | 0.1% |  | 7.9V | 50V
1 | 11 | RESISTOR_0603_2.74K | R4 | 1000 |  | P20020CT-ND | Panasonic Electronic Components | 667-ERJ-PB3B2741V | ERJ-PB3B2741V | 0.2W | 2.74k | 0.1% |  | 23.41V | 150V
1 | 11 | RESISTOR_0603_20K | R14 | 1000 |  | 311-20.0KHRTR-ND | Yageo | 603-RC0603FR-0720KL | RC0603FR-0720KL | 0.1 W | 20k | 1% |  | 44.72V | 75V
1 | 11 | RESISTOR_0603_2K | R22 | 1000 |  | 10-ERJ-UP3F2001VTR-ND | Panasonic Electronic Components | 667-ERJ-UP3F2001V | ERJ-UP3F2001V | 0.25W | 2k | 1% |  | 22.36V | 150V
1 | 11 | RESISTOR_0603_3.32K | R2 | 1000 |  | YAG1651TR-ND | Yageo | 603-RT0603BRD073K32L | RT0603BRD073K32L | 0.1W | 3.32k | 0.1% |  | 18.22V | 75V
3 | 13 | RESISTOR_0603_7.5K | R3, R6, R12 | 333 |  | P20072CT-ND | Panasonic Electronic Components | 667-ERJ-PB3B7501V | ERJ-PB3B7501V | 0.2W | 7.5k | 0.1% |  | 38.73V | 150V
1 | 11 | RESISTOR_0603_DNP | R15 | 1000 |  |  |  |  |  |  | DNP
1 | 3 | VOLTAGE_REFERENCE_SOIC-8_10V | U6 | 200 |  | MAX6176AASA+-ND | Maxim Integrated | 700-MAX6176AASA | MAX6176AASA+
1 | 3 | VOLTAGE_REGULATOR_SOT-223_3.3V | U7 | 200 |  | LMS8117AMP-3.3/NOPBCT-ND | Texas Instruments | 926-LMS8117AMP33NOPB | LMS8117AMP-3.3/NOPB

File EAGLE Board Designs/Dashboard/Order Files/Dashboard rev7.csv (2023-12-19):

Board Quantity | Ordering Quantity | Value | Reference | ATTRITION | CAPACITANCE | COLOR | CURRENT | DKPN | FREQUENCY | FUSE_TYPE | GAUGE | MANUFACTURER | MOPN | MPN | POWER | RESISTANCE | TOLERANCE | VOLTAGE | VOLTAGE_CONTINUOUS | VOLTAGE_MAX | VOLUME
1 | 3 | 24_MHZ_XTAL_OSCILLATOR | X1 | 200 |  |  |  | FL2400022CT-ND |  |  |  |  | 729-FL2400022 | FL2400022
1 | 3 | BUTTON | S1 | 200 |  |  |  | SW415-ND |  |  |  | Omron | 653-B3S-1000 | B3S-1000
1 | 3 | BUZZER_3_PIN_CPT-3011C-120 | LS100 | 200 |  |  |  | 102-3762-ND | 3kHz |  |  | CUI Devices | 490-CPT-3011C-120 | CPT-3011C-120 |  |  |  | 12V |  |  | 85dB
19 | 29 | CAPACITOR_0603_10V_0.1UF | C4, C5, C6, C7, C9, C10, C11, C12, C14, C16, C18, C19, C20, C21, C26, C27, C28, C34, C38 | 53 | 0.1µF |  |  | 720-1688-1-ND |  |  |  | Vishay Vitramon | 77-VJ0603Y104JXQPBC | VJ0603Y104JXQPW1BC |  |  | 5% | 10V
2 | 12 | CAPACITOR_0603_10V_15PF | C1, C2 | 500 | 15pF |  |  | 720-VJ0603A150FXQPW1BCCT-ND |  |  |  | Vishay Vitramon | 77-VJ0603A150FXQPBC | VJ0603A150FXQPW1BC |  |  | 1% | 10V
2 | 12 | CAPACITOR_0603_10V_1UF | C13, C39 | 500 | 1µF |  |  | 311-1796-1-ND |  |  |  | Yageo | 603-CC603KRX7R6BB105 | CC0603KRX7R6BB105 |  |  | 10% | 10V
1 | 11 | CAPACITOR_0603_10V_4.7NF | C25 | 1000 | 4.7nF |  |  | 732-7931-1-ND |  |  |  | Würth Elektronik | 710-885012206012 | 885012206012 |  |  | 10% | 10V
3 | 13 | CAPACITOR_0603_10V_4.7UF | C3, C22, C29 | 333 | 4.7µF |  |  | 1276-1044-1-ND |  |  |  | Samsung Electro-Mechanics | 187-CL10A475KP8NNNC | CL10A475KP8NNNC |  |  | 10% | 10V
1 | 11 | CAPACITOR_0603_25V_0.1UF | C15 | 1000 | 0.1µF |  |  | 1276-1006-1-ND |  |  |  | Samsung Electro-Mechanics | 187-CL10B104KA8NNNC | CL10B104KA8NNNC |  |  | 10% | 25V
1 | 11 | CAPACITOR_0603_25V_1.2NF | C17 | 1000 | 1.2nF |  |  | 311-4079-2-ND |  |  |  | YAGEO | 603-CC603KRX7R8BB122 | CC0603KRX7R8BB122 |  |  | 10% | 25V
1 | 11 | CAPACITOR_0603_25V_10UF | C33 | 1000 | 10µF |  |  | 490-7202-1-ND |  |  |  | Murata Electronics | 81-GRM188R61E106MA3D | GRM188R61E106MA73D |  |  | 20% | 25V
3 | 13 | CAPACITOR_0805_50V_10UF | C8, C24, C40 | 333 | 10uF |  |  | 490-18663-2-ND |  |  |  | Murata | 81-GRM21BR61H106KE3L | GRM21BR61H106KE43L |  |  | 10% | 50V
2 | 4 | CONNECTOR-10__ | J5, J10 | 100 |  |  |  | WM12366CT-ND |  |  |  | MOLEX | 538-505110-1092 | 5051101092
2 | 4 | CONNECTOR-4_FD19_0492_ | J7, J9 | 100 |  |  |  | WM12360CT-ND |  |  |  | Molex | 538-505110-0492 | 505110-0492
2 | 4 | CONNECTOR-4_μF_S_RA_ | J1, J3 | 100 |  |  |  | WM1832CT-ND |  |  |  | Molex | 538-0430450411 | 0430450411
1 | 3 | CONNECTOR-6_μF_S_RA_ | J4 | 200 |  |  |  | WM1833CT-ND |  |  |  | Molex | 538-43045-0611 | 0430450611
2 | 4 | CONNECTOR-8_μF_S_RA_ | J2, J11 | 100 |  |  |  | WM1834CT-ND |  |  |  | Molex | 538-43045-0811 | 0430450811
18 | 36 | CRIMP_MICROFIT_20-24 | O6, O7, O8, O9, O10, O11, O12, O13, O14, O15, O16, O17, O18, O19, O20, O21, O22, O23 | 100 |  |  |  | WM2776CT-ND |  |  | 20-24 | Molex | 538-43030-0003 | 0430300003
1 | 3 | FUSE_HOLDER_MINIBLADESMD | XF1 | 200 |  |  |  | 36-3588-ND |  | MINI 297 |  | Keystone Electronics | 534-3588 | 3588
1 | 2 | FUSE_MINI_BLADE_2 | O4 | 100 |  |  | 2A | F986-ND |  | MINI 297 |  | Littelfuse Inc. | 576-0297002.WXNV | 0297002.WXNV
1 |  | JUMPER_3PIN | U$12
1 | 11 | LED_0603_BLUE | 5V | 1000 |  | Blue |  | 754-1789-1-ND |  |  |  | Kingbright | 604-APT1608VBC/D | APT1608VBC/D
2 | 12 | LED_0603_GREEN_2V2 | 3V3, MCU_LED | 500 |  | Green |  | 754-1121-1-ND |  |  |  | Kingbright | 604-APT1608SGC | APT1608SGC
1 | 11 | LED_0603_ORANGE | 24V | 1000 |  | Orange |  | 754-1120-1-ND |  |  |  | Kingbright | 604-APT1608SECK | APT1608SECK
1 | 11 | LED_0603_RED | 12V | 1000 |  | Red |  | 754-1786-1-ND |  |  |  | Kingbright | 604-APT1608SECKJ3PRV | APT1608SECK/J3-PRV
1 | 3 | LED_7_SEGMENT_BLUE_DSM7TA | D101 | 200 |  | Blue |  | DSM7TA56106TTR-ND |  |  |  | Visual Communications Company | 593-DSM7TA56106T | DSM7TA56106T
1 | 3 | MCP23S08 | U3 | 200 |  |  |  | MCP23S08-E/SS-ND |  |  |  | Microchip Technology | 579-MCP23S08-E/SS | MCP23S08-E/SS
12 | 14 | NEOPIXEL_IN-PI55QATPRPGPBPW-40 | U1, U2, U4, U6, U7, U8, U9, U10, U12, U13, U14, U15 | 17 |  |  |  | 1830-1210-2-ND |  |  |  | Inolux | 743-I55QATPRPGPBPW40 | IN-PI55QATPRPGPBPW-40
1 | 3 | RE46C100 | U5 | 200 |  |  |  | RE46C100S8TFTR-ND |  |  |  | Microchip Technology | 579-RE46C100S8TF | RE46C100S8TF
1 | 2 | RECEPTACLE-4_MICROFIT | O1 | 100 |  |  |  | WM11225-ND |  |  |  | Molex | 538-43025-0408 | 0430250408
1 | 2 | RECEPTACLE-6_MICROFIT | O2 | 100 |  |  |  | WM13209-ND |  |  |  | Molex | 538-43025-0608 | 0430250608
1 | 2 | RECEPTACLE-8_MICROFIT | O3 | 100 |  |  |  | WM13210-ND |  |  |  | Molex | 538-43025-0808 | 0430250808
1 | 11 | RESISTOR_0603_0 | R15 | 1000 |  |  |  | 311-0.0HRCT-ND |  |  |  | Yageo | 603-RC0603FR-070RL | RC0603FR-070RL | 0.1W | 0 | 1% |  | 75V | 75V
1 | 11 | RESISTOR_0603_1.5M | R13 | 1000 |  |  |  | 311-1.50MHRCT-ND |  |  |  | Yageo | 603-RC0603FR-071M5L | RC0603FR-071M5L | 0.1W | 1.5M | 1% |  | 75V | 75V
3 | 13 | RESISTOR_0603_10K | R7, R11, R16 | 333 |  |  |  | P10KBDCT-ND |  |  |  | Panasonic Electronic Components | 667-ERA-3ARB103V | ERA-3ARB103V | 0.1W | 10k | 0.1% |  | 31.62V | 75V
1 | 11 | RESISTOR_0603_150K | R9 | 1000 |  |  |  | P150KDBCT-ND |  |  |  | Panasonic Electronic Components | 667-ERA-3AEB154V | ERA-3AEB154V | 0.1W | 150k | 1% |  | 75V | 75V
1 | 11 | RESISTOR_0603_180 | R21 | 1000 |  |  |  | 311-180HRCT-ND |  |  |  | Yageo | 603-RC0603FR-07180RL | RC0603FR-07180RL | 0.1W | 180 | 1% |  | 4.24V | 75V
1 | 11 | RESISTOR_0603_1K | R2 | 1000 |  |  |  | 1712-CPF-A-0603B1K0ETR-ND |  |  |  | TE Connectivity Passive Product | 279-CPF-A-0603B1K0E | CPF-A-0603B1K0E | 0.0625W | 1k | 0.1% |  | 7.9V | 50V
2 | 12 | RESISTOR_0603_240 | R1, R6 | 500 |  |  |  | 311-240HRCT-ND |  |  |  | Yageo | 603-RC0603FR-07240RL | RC0603FR-07240RL | 0.1W | 240 | 1% |  | 4.90V | 75V
1 | 11 | RESISTOR_0603_3.3K | R83 | 1000 |  |  |  | P20340TR-ND |  |  |  | Panasonic Electronic Components | 667-ERJ-PB3D3301V | ERJ-PB3D3301V | 0.3W | 3.3k | 0.5% |  | 25.69V | 150
2 | 12 | RESISTOR_0603_30 | R19, R20 | 500 |  |  |  | 10-ERJ-UP3F30R0VCT-ND |  |  |  | Panasonic Electronic Components | 667-ERJ-UP3F30R0V | ERJ-UP3F30R0V | 0.25W | 30 | 1% |  | 2.74V | 150
3 | 13 | RESISTOR_0603_41.2K | R3, R4, R5 | 333 |  |  |  | P20155CT-ND |  |  |  | Panasonic Electronic Components | 667-ERJ-PB3B4122V | ERJ-PB3B4122V | 0.2W | 41.2k | 0.1% |  | 150V | 200V
5 | 15 | RESISTOR_0603_5.1K | R8, R12, R14, R17, R18 | 200 |  |  |  | 311-5.10KHRTR-ND |  |  |  | Yageo | 603-RC0603FR-075K1L | RC0603FR-075K1L | 0.1W | 5.1k | 1% |  | 22.58V | 75V
2 | 12 | RESISTOR_0603_60.4 | R36, R60 | 500 |  |  |  | 311-60.4HRCT-ND |  |  |  | Yageo | 603-RC0603FR-0760R4L | RC0603FR-0760R4L | 0.1W | 60.4 | 1% |  | 2.48V | 75V
2 | 4 | RESISTOR_NETWORK_4_160 | RN2, RN4 | 100 |  |  |  | YC164J-160CT-ND |  |  |  | Yageo | 603-YC164-JR-07160RL | YC164-JR-07160RL | 1/16W | 160 | 5% | 50V
1 | 3 | SCHOTTKY__15V | D2 | 200 |  |  | 1A | 150-LSM115JE3/TR13CT-ND |  |  |  | Microchip Technology | 494-LSM115JE3/TR13 | LSM115JE3/TR13 |  |  |  | 15V
1 | 3 | SN74LXC2T45DCUR | U$6 | 200 |  |  |  | 296-SN74LXC2T45DCUR* |  |  |  | Texas Instruments | 595-SN74LXC2T45DCUR | SN74LXC2T45DCUR
1 | 3 | STM32-LQFP64 | U16 | 200 |  |  |  | 497-15376-ND |  |  |  | STMicroelectronics | 511-STM32F446RET6 | STM32F446RET6
1 | 3 | SWITCH_SPDT_SSSS916400 | S2 | 200 |  |  |  | 4809-SSSS916400-ND |  |  |  | Alps Alpine | 688-SSSS916400 | SSSS916400
1 | 3 | TCAN1051HQV-Q1 | U27 | 200 |  |  |  | 296-49935-1-ND |  |  |  | Texas Instruments | 595-TCAN1051HGVDQ1 | TCAN1051HGVDRQ1
13 | 15 | TEST_POINT | BOTS, BRB, INERTIA, NEOPIXELS, SPI1_MOSI, SPI1_SCK, SPI3_MOSI, SPI3_SCK, TP_3.3V, TP_5V, TP_12V, TP_24V, TP_GND | 15 |  |  |  | 36-5015CT-ND |  |  |  | Keystone Electronics | 534-5015 | 5015
4 | 6 | TVS_DO-214AA_30V | D3, D4, D5, D6 | 50 |  |  |  | 118-1.5SMBJ30ATR-ND |  |  |  | Bourns Inc. | 652-1.5SMBJ30A | 1.5SMBJ30A |  |  |  | 30V
1 | 3 | USB4110 | J8 | 200 |  |  |  | 2073-USB4110-GF-A-1-ND |  |  |  | GCT | 640-USB4110-GF-A | USB4110
1 | 3 | USBLC6-2SC6 | D1 | 200 |  |  |  | 497-5235-1-ND |  |  |  | STMicroelectronics | 511-USBLC6-2SC6 | USBLC6-2SC6
1 | 3 | VOLTAGE_REGULATOR_MODULE__12V | A2 | 200 |  |  |  | 811-3294-ND |  |  |  | Murata Power Solutions Inc. | 580-OKI78SR12/1W36HC | OKI-78SR-12/1.0-W36H-C
1 | 3 | VOLTAGE_REGULATOR_MODULE__5V | A1 | 200 |  |  |  | 811-2692-ND |  |  |  | Murata Power Solutions Inc. | 580-OKI78SR51.5W36HC | OKI-78SR-5/1.5-W36H-C
1 | 3 | VOLTAGE_REGULATOR_SOT-223_3.3V | U17 | 200 |  |  |  | LMS8117AMP-3.3/NOPBCT-ND |  |  |  | Texas Instruments | 926-LMS8117AMP33NOPB | LMS8117AMP-3.3/NOPB

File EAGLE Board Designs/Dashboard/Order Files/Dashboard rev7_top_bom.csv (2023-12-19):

Comment | Designator | Footprint | LCSC Part #
24_MHZ_XTAL_OSCILLATOR | X1 | 24_MHZ_XTAL_OSCILLATOR
BUTTON | S1 | B3S-100X
CAPACITOR_0603_10V_0.1UF | C4 C5 C6 C7 C9 C10 C11 C12 C14 C16 C18 C19 C20 C21 C26 C27 C28 C34 C38 | 0603-CAP
CAPACITOR_0603_10V_1UF | C13 C39 | 0603-CAP
CAPACITOR_0603_10V_4.7NF | C25 | 0603-CAP
CAPACITOR_0603_10V_4.7UF | C3 C22 C29 | 0603-CAP
CAPACITOR_0603_10V_15PF | C1 C2 | 0603-CAP
CAPACITOR_0603_25V_0.1UF | C15 | 0603-CAP
CAPACITOR_0603_25V_1.2NF | C17 | 0603-CAP
CAPACITOR_0603_25V_10UF | C33 | 0603-CAP
CAPACITOR_0805_50V_10UF | C8 C24 C40 | 0805-CAP
CONNECTOR-4_FD19_0492_ | J7 J9 | 5051100492
CONNECTOR-4_μF_S_RA_ | J1 J3 | MOLEX_MICROFIT_SMD_RIGHTANGLE_04_DUAL
CONNECTOR-6_μF_S_RA_ | J4 | MOLEX_MICROFIT_SMD_RIGHTANGLE_06_DUAL
CONNECTOR-8_μF_S_RA_ | J2 J11 | MOLEX_MICROFIT_SMD_RIGHTANGLE_08_DUAL
CONNECTOR-10__ | J5 J10 | 5051101092
FUSE_HOLDER_MINIBLADESMD | XF1 | 3588
LED_0603_BLUE | 5V | 0603-LED
LED_0603_GREEN_2V2 | 3V3 MCU_LED | 0603-LED
LED_0603_ORANGE | 24V | 0603-LED
LED_0603_RED | 12V | 0603-LED
MCP23S08 | U3 | SSOP-20
RE46C100 | U5 | SOIC-08(NARROW 0.15")
RESISTOR_0603_0 | R15 | 0603-RES
RESISTOR_0603_1.5M | R13 | 0603-RES
RESISTOR_0603_1K | R2 | 0603-RES
RESISTOR_0603_3.3K | R83 | 0603-RES
RESISTOR_0603_5.1K | R8 R12 R14 R17 R18 | 0603-RES
RESISTOR_0603_10K | R7 R11 R16 | 0603-RES
RESISTOR_0603_30 | R19 R20 | 0603-RES
RESISTOR_0603_41.2K | R3 R4 R5 | 0603-RES
RESISTOR_0603_60.4 | R36 R60 | 0603-RES
RESISTOR_0603_150K | R9 | 0603-RES
RESISTOR_0603_180 | R21 | 0603-RES
RESISTOR_0603_240 | R1 R6 | 0603-RES
RESISTOR_NETWORK_4_160 | RN2 RN4 | 1206-RES-ARRAY
SCHOTTKY__15V | D2 | DO-214BA
SN74LXC2T45DCUR | U$6 | 8-VSSOP
STM32-LQFP64 | U16 | STM32-FOOTPRINT
TCAN1051HQV-Q1 | U27 | SOIC-08(NARROW 0.15")
TEST_POINT | BOTS BRB INERTIA NEOPIXELS SPI1_MOSI SPI1_SCK SPI3_MOSI SPI3_SCK TP_3.3V TP_5V TP_12V TP_24V TP_GND | 5015
TVS_DO-214AA_30V | D3 D4 D5 D6 | DO-214AA
USB4110 | J8 | USB4110
USBLC6-2SC6 | D1 | SOT-23-6
VOLTAGE_REGULATOR_SOT-223_3.3V | U17 | SOT-223

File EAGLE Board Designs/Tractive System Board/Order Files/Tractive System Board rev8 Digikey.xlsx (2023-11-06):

Digi-Key Part Number | Manufacturer | Manufacturer Part Number | Requested Part Number | Description | Customer Reference | Quantity 1 | Unit Price 1 | Extended Price 1 | Quantity 2 | Unit Price 2 | Extended Price 2 | Minimum Order Quantity | Availability | Manufacturer Lead Time | Country of Origin | RoHS Status | Lead Free Status | REACH Status | Pricing Valid Through
296-AMC3330DWERCT-ND | TEXAS INSTRUMENTS | AMC3330DWER | 296-AMC3330DWERCT-ND | 1-V INPUT, PRECISION REINFORCED | U7, U8 | 2 | 9.74000 | $19.48 | 4 | 9.74000 | $38.96 | 1 | 1297 | 12 Weeks | Taiwan | ROHS3 Compliant | Not available | REACH Unaffected | 11/30/2023
311-1788-1-ND | YAGEO | CC0603KRX7R0BB103 | 311-1788-1-ND | CAP CER 10000PF 100V X7R 0603 | C43, C52 | 2 | 0.09000 | $0.18 | 12 | 0.04800 | $0.58 | 1 | 52672 | 16 Weeks | Taiwan | ROHS3 Compliant | Lead free | REACH Unaffected | 11/30/2023
720-1688-1-ND | VISHAY VITRAMON | VJ0603Y104JXQPW1BC | 720-1688-1-ND | CAP CER 0.1UF 10V X7R 0603 | C23, C25 | 2 | 0.17000 | $0.34 | 12 | 0.11400 | $1.37 | 1 | 15801 | 22 Weeks | China | ROHS3 Compliant | Lead free | - | 11/30/2023
490-7202-1-ND | MURATA ELECTRONICS | GRM188R61E106MA73D | 490-7202-1-ND | CAP CER 10UF 25V X5R 0603 | C24, C32, C33 | 3 | 0.24000 | $0.72 | 13 | 0.15900 | $2.07 | 1 | 2812220 | 19 Weeks | Japan | ROHS3 Compliant | Lead free | REACH Unaffected | 11/30/2023
1276-1184-1-ND | SAMSUNG ELECTRO-MECHANICS AMERICA, INC | CL10B105KA8NNNC | 1276-1184-1-ND | CAP CER 1UF 25V X7R 0603 | C40, C49 | 2 | 0.09000 | $0.18 | 12 | 0.03800 | $0.46 | 1 | 1584422 | 22 Weeks | China | ROHS3 Compliant | Lead free | REACH Unaffected | 11/30/2023
478-KAF15AR71E473KTCT-ND | KYOCERA AVX COMPONENTS CORPORATION | KAF15AR71E473KT | 478-KAF15AR71E473KTCT-ND | CAP CER 0.047UF 25V X7R 0603 | C30 | 1 | 0.28000 | $0.28 | 11 | 0.19500 | $2.15 | 1 | 27861 | 12 Weeks | El Salvador | ROHS3 Compliant | Lead free | REACH Unaffected | 11/30/2023
311-1344-1-ND | YAGEO | CC0603KRX7R9BB104 | 311-1344-1-ND | CAP CER 0.1UF 50V X7R 0603 | C26, C37, C42, C46, C51 | 5 | 0.09000 | $0.45 | 15 | 0.04900 | $0.74 | 1 | 4792591 | 16 Weeks | Taiwan | ROHS3 Compliant | Lead free | REACH Unaffected | 11/30/2023
445-7404-1-ND | TDK CORPORATION | C1608C0G1H103J080AA | 445-7404-1-ND | CAP CER 10000PF 50V C0G 0603 | C56 | 1 | 0.25000 | $0.25 | 11 | 0.16700 | $1.84 | 1 | 345229 | 28 Weeks | Japan | ROHS3 Compliant | Lead free | REACH Unaffected | 11/30/2023
399-C0603C102K5RAC7867CT-ND | KEMET | C0603C102K5RAC7867 | 399-C0603C102K5RAC7867CT-ND | CAP CER 1000PF 50V X7R 0603 | C41, C50 | 2 | 0.09000 | $0.18 | 12 | 0.04600 | $0.55 | 1 | 7473835 | 22 Weeks | Taiwan | ROHS3 Compliant | Lead free | REACH Unaffected | 11/30/2023
587-2400-1-ND | TAIYO YUDEN | UMK107BJ105KA-T | 587-2400-1-ND | CAP CER 1UF 50V X5R 0603 | C27 | 1 | 0.15000 | $0.15 | 11 | 0.10300 | $1.13 | 1 | 3132244 | 58 Weeks | China | ROHS3 Compliant | Lead free | - | 11/30/2023
478-KGM31HR71E105KUCT-ND | KYOCERA AVX COMPONENTS CORPORATION | KGM31HR71E105KU | 478-KGM31HR71E105KUCT-ND | CAP CER 1UF 25V X7R 1206 | C36, C45 | 2 | 0.29000 | $0.58 | 12 | 0.19800 | $2.38 | 1 | 983531 | 16 Weeks | Taiwan | ROHS3 Compliant | Lead free | REACH Unaffected | 11/30/2023
445-14655-1-ND | TDK CORPORATION | C3216NP01H104J160AA | 445-14655-1-ND | CAP CER 0.1UF 50V NP0 1206 | C39, C48 | 2 | 0.57000 | $1.14 | 12 | 0.39800 | $4.78 | 1 | 37810 | 24 Weeks | Japan | ROHS3 Compliant | Lead free | REACH Unaffected | 11/30/2023
478-KGM31BR71H102KTCT-ND | KYOCERA AVX COMPONENTS CORPORATION | KGM31BR71H102KT | 478-KGM31BR71H102KTCT-ND | CAP CER 1000PF 50V X7R 1206 | C31, C38, C44, C47 | 4 | 0.22000 | $0.88 | 14 | 0.14800 | $2.07 | 1 | 32790 | 12 Weeks | China | ROHS3 Compliant | Lead free | REACH Unaffected | 11/30/2023
445-9083-1-ND | TDK CORPORATION | CGA5L4C0G2J103J160AA | 445-9083-1-ND | CAP CER 10000PF 630V C0G 1206 | C55 | 1 | 0.36000 | $0.36 | 11 | 0.25400 | $2.79 | 1 | 62958 | 28 Weeks | Japan | ROHS3 Compliant | Lead free | REACH Unaffected | 11/30/2023
490-5041-1-ND | MURATA ELECTRONICS | GCM31A7U2J470JX01D | 490-5041-1-ND | CAP CER 47PF 630V U2J 1206 | C54 | 1 | 0.39000 | $0.39 | 11 | 0.27600 | $3.04 | 1 | 9848 | 25 Weeks | Japan | ROHS3 Compliant | Lead free | REACH Unaffected | 11/30/2023
399-C1812W104KDRAC7800CT-ND | KEMET | C1812W104KDRAC7800 | 399-C1812W104KDRAC7800CT-ND | CAP CER 0.1UF 1KV X7R 1812 | C35 | 1 | 0.98000 | $0.98 | 3 | 0.98000 | $2.94 | 1 | 0 | 36 Weeks | Mexico | ROHS3 Compliant | Lead free | REACH Unaffected | 11/30/2023
445-CGA9N1X7R1V476M230KCCT-ND | TDK CORPORATION | CGA9N1X7R1V476M230KC | 445-CGA9N1X7R1V476M230KCCT-ND | CAP CER 47UF 35V X7R 2220 | C3 | 1 | 4.13000 | $4.13 | 3 | 4.13000 | $12.39 | 1 | 150 | 28 Weeks | Japan | ROHS3 Compliant | Not available | REACH Unaffected | 11/30/2023
WM20164-ND | MOLEX, LLC | 0436500617 | WM20164-ND | CONN HEADER VERT 6POS 3MM | J2 | 1 | 2.37000 | $2.37 | 3 | 2.37000 | $7.11 | 1 | 1024 | 9 Weeks | Mexico | ROHS3 Compliant | Lead free | REACH Unaffected | 11/30/2023
WM2477-ND | MOLEX, LLC | 0436500716 | WM2477-ND | CONN HEADER VERT 7POS 3MM | J1 | 1 | 2.08000 | $2.08 | 10 | 1.77200 | $17.72 | 1 | 2186 | 7 Weeks | Mexico | ROHS3 Compliant | Lead free | REACH Unaffected | 11/30/2023
WM1798-ND | MOLEX, LLC | 0430450814 | WM1798-ND | CONN HEADER VERT 8POS 3MM | J3 | 1 | 2.92000 | $2.92 | 3 | 2.92000 | $8.76 | 1 | 3585 | 21 Weeks | Mexico | ROHS3 Compliant | Lead free | REACH Unaffected | 11/30/2023
WM2776CT-ND | MOLEX, LLC | 0430300003 | WM2776CT-ND | CONN SOCKET 20-24AWG CRIMP GOLD | O9, O10, O11, O12, O13, O14, O15, O16, O17, O18, | 14 | 0.14000 | $1.96 | 28 | 0.14000 | $3.92 | 10 | 136066 | 4 Weeks | United States | ROHS3 Compliant | Lead free | REACH Unaffected | 11/30/2023
F3783-ND | LITTELFUSE INC | 01220088Z | F3783-ND | FUSE CLIP CARTRIDGE 1KV 30A PCB | F1, F2 | 2 | 0.77000 | $1.54 | 10 | 0.69400 | $6.94 | 1 | 19045 | 10 Weeks | China | ROHS3 Compliant | Lead free | REACH Unaffected | 11/30/2023
SRR0745A-102MCT-ND | BOURNS INC | SRR0745A-102M | SRR0745A-102MCT-ND | FIXED IND 1MH 200MA 4.1 OHM SMD | L1 | 1 | 0.83000 | $0.83 | 5 | 0.83000 | $4.15 | 1 | 99676 | 14 Weeks | China | ROHS3 Compliant | Lead free | REACH Unaffected | 11/30/2023
754-1789-1-ND | KINGBRIGHT AMERICA LLC | APT1608VBC/D | 754-1789-1-ND | LED BLUE CLEAR CHIP SMD | D3, D4 | 2 | 0.47000 | $0.94 | 12 | 0.30800 | $3.70 | 1 | 47260 | 8 Weeks | China | ROHS3 Compliant | Not available | REACH Unaffected | 11/30/2023
754-1790-1-ND | KINGBRIGHT AMERICA LLC | APT1608ZGCK | 754-1790-1-ND | LED GREEN CLEAR CHIP SMD | D6, LED_+12V1 | 2 | 0.54000 | $1.08 | 12 | 0.33100 | $3.97 | 1 | 207253 | 8 Weeks | China | ROHS3 Compliant | Not available | REACH Unaffected | 11/30/2023
754-1120-1-ND | KINGBRIGHT AMERICA LLC | APT1608SECK | 754-1120-1-ND | LED ORANGE CLEAR CHIP SMD | D5 | 1 | 0.27000 | $0.27 | 11 | 0.20700 | $2.28 | 1 | 41523 | 8 Weeks | China | ROHS3 Compliant | Not available | REACH Unaffected | 11/30/2023
754-1788-1-ND | KINGBRIGHT AMERICA LLC | APT1608SYCK/J3-PRV | 754-1788-1-ND | LED YELLOW CLEAR CHIP SMD | D8 | 1 | 0.54000 | $0.54 | 11 | 0.33100 | $3.64 | 1 | 37015 | 8 Weeks | China | ROHS3 Compliant | Not available | REACH Unaffected | 11/30/2023
505-LT8315HFE#PBF-ND | ANALOG DEVICES INC | LT8315HFE#PBF | 505-LT8315HFE#PBF-ND | IC REG FLYBACK 800MA 20TSSOP | U6 | 1 | 10.81000 | $10.81 | 5 | 10.81000 | $54.05 | 1 | 67 | 13 Weeks | Thailand | ROHS3 Compliant | Not available | REACH Unaffected | 11/30/2023
505-LTC6994CS6-2#TRMPBFCT-ND | ANALOG DEVICES INC | LTC6994CS6-2#TRMPBF | 505-LTC6994CS6-2#TRMPBFCT-ND | IC DELAY BLOCK 8TAP PROG TSOT23 | U10 | 1 | 4.15000 | $4.15 | 3 | 4.15000 | $12.45 | 1 | 10050 | 13 Weeks | Malaysia | ROHS3 Compliant | Not available | REACH Unaffected | 11/30/2023
WM11225-ND | MOLEX, LLC | 0430250408 | WM11225-ND | CONN RCPT HSG 4POS 3.00MM | O23 | 1 | 0.44000 | $0.44 | 2 | 0.44000 | $0.88 | 1 | 30934 | 13 Weeks | China | ROHS3 Compliant | Lead free | REACH Unaffected | 11/30/2023
WM13217-ND | MOLEX, LLC | 0436450608 | WM13217-ND | CONN RCPT HSG 6POS 3.00MM | O3 | 1 | 0.51000 | $0.51 | 2 | 0.51000 | $1.02 | 1 | 11533 | 11 Weeks | United States | ROHS3 Compliant | Lead free | REACH Unaffected | 11/30/2023
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

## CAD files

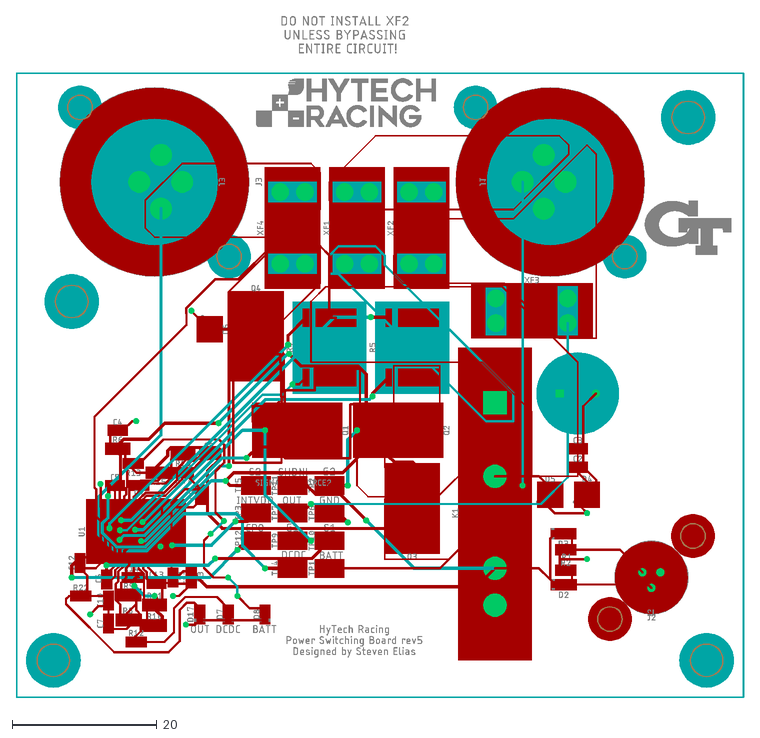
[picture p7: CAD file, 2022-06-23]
EAGLE Board Designs/Power Switching Board/Order Files/Power Switching Circuit rev5.dxf
100.5 x 94.1

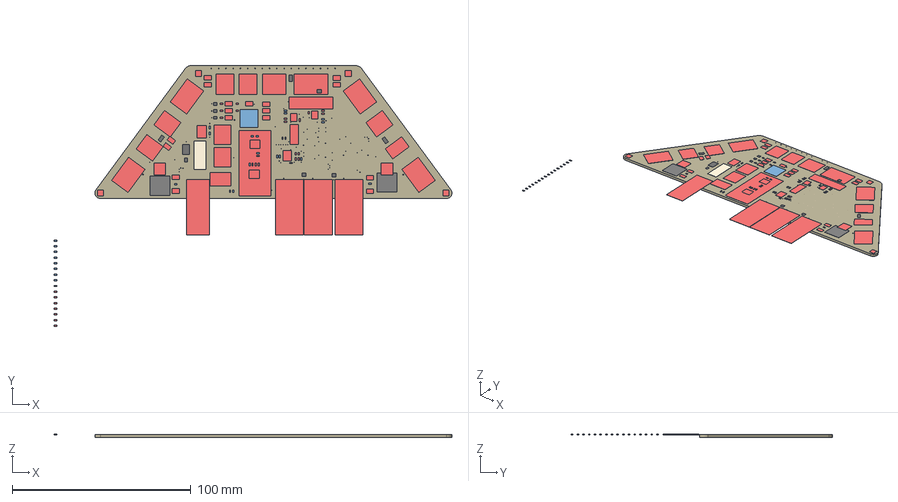
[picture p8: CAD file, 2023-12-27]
EAGLE Board Designs/Sensor Acquisition Board/Board step files/SAB_moved_MH.step
222.4 x 145.8 x 1.77 mm
Board
VOLTAGE_REGULATOR_MODULE_OKI-78SR_5V x 2
TEENSY_4.0SM
CAPACITOR_0805_50V_10UF x 3
CAPACITOR_0603_10V_1UF x 33
CAPACITOR_ELECTROLYTIC_EEH_AZS_470UF
TVS_DO-214AA_30V
TVS_DO-219AB_14V
TVS_BIDIRECTIONAL_DUAL x 4
TVS_BIDIRECTIONAL_DUALRS422 x 2
LED_0603_GREEN x 3
SCHOTTKY_1206_40V
CONNECTOR-2_MICROFIT_SMD_RIGHTANGLE_02_SINGLE_BLACK
CONNECTOR-6_μF_T_V_BLACK
CONNECTOR-8_μF_T_V_BLACK x 4
CONNECTOR-4_μF_T_V_BLACK x 5
CONNECTOR-10_MF_T_V_
CONNECTOR-4_μF_S_RA_ x 3
RESISTOR_0603_8.35K x 28
78613/3C_78613/3C x 2
TEST_POINT x 17
VOLTAGE_REGULATOR_SOT-223_3.3V
LTC6820 x 2
MAX3075 x 2
MCP3208
MAX3227
FUSE_HOLDER_MINIBLADESMD
LOGO_HYTECH_MEDIUM
LOGO_GT_MEDIUM
MOUNTING_M3 x 4
CONNECTOR-2_μF_T_V_BLACK
LOGO_HYTECH_SQUARE_LARGE x 2

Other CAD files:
EAGLE Board Designs/Dashboard/Dashboard rev6.dxf

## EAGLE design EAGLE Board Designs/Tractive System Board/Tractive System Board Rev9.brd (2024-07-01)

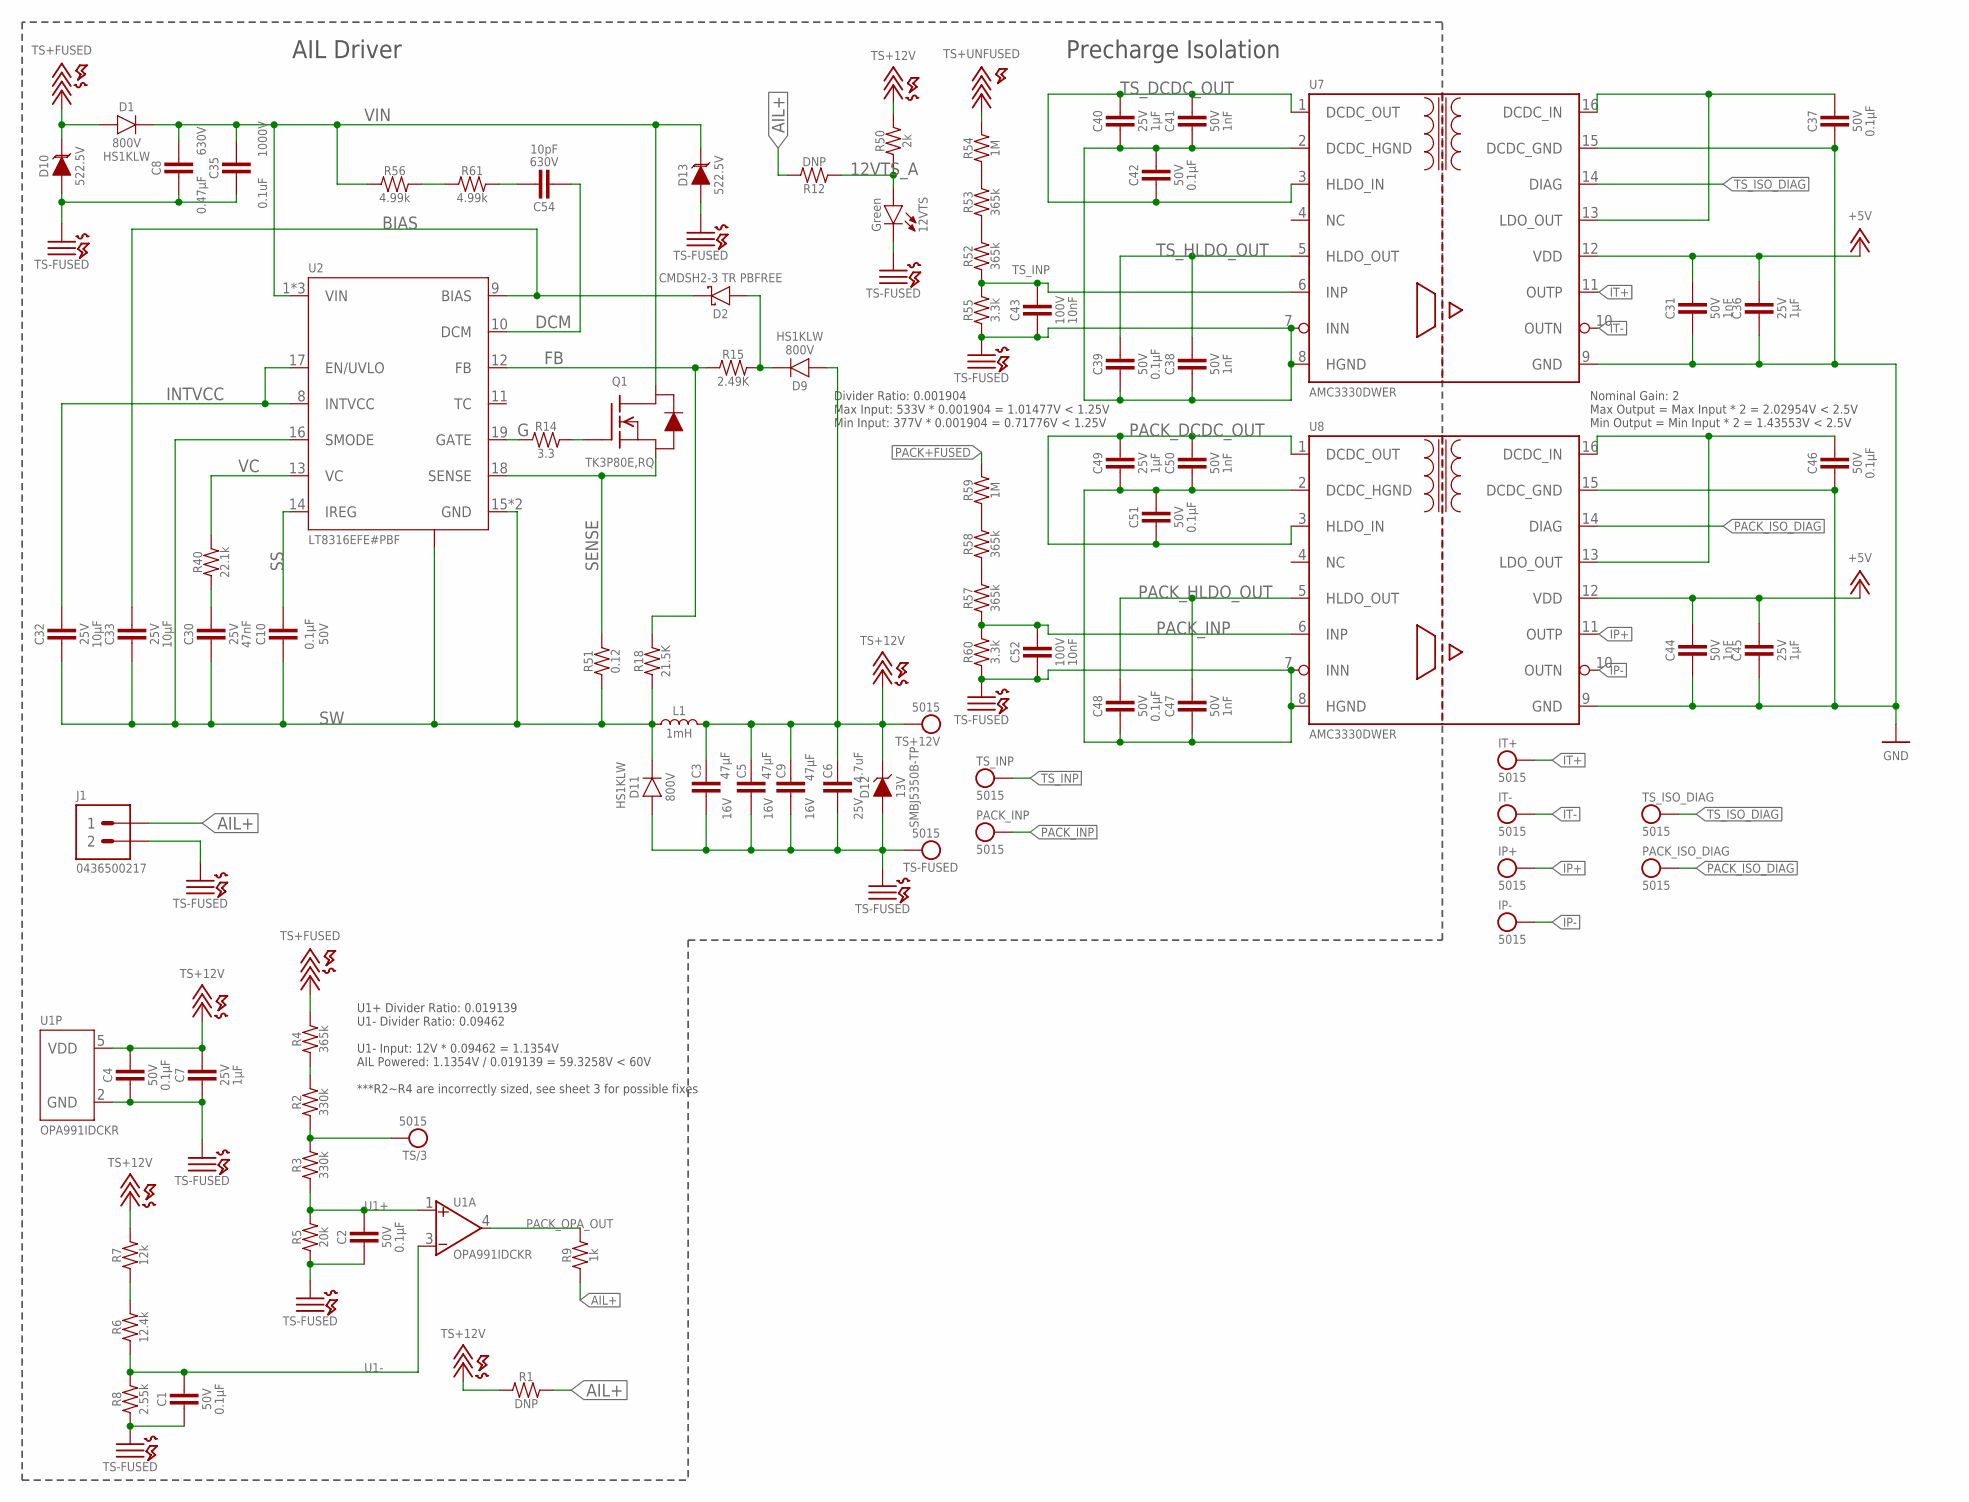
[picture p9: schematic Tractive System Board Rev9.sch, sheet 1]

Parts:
12VTS: LED_0603_GREEN; 0603-LED
C1, C2, C4, C10, C37, C42, C46, C51: CAPACITOR_0603_50V_0.1UF; 0603-CAP
C3, C5, C9: CAPACITOR_1206_16V_47UF; 1206-CAP
C6: CAPACITOR_0603_25V_4.7UF; 0603-CAP
C7, C40, C49: CAPACITOR_0603_25V_1UF; 0603-CAP
C8: CAPACITOR_2220_630V_0.47UF; 2220-CAP
C30: CAPACITOR_0603_25V_47NF; 0603-CAP
C31, C38, C44, C47: CAPACITOR_1206_50V_1NF; 1206-CAP
C32, C33: CAPACITOR_0603_25V_10UF; 0603-CAP
C35: CAPACITOR_1812_1000V_0.1UF; 1812-CAP
C36, C45: CAPACITOR_1206_25V_1UF; 1206-CAP
C39, C48: CAPACITOR_1206_50V_0.1UF; 1206-CAP
C41, C50: CAPACITOR_0603_50V_1NF; 0603-CAP
C43, C52: CAPACITOR_0603_100V_10NF; 0603-CAP
C54: CAPACITOR_1206_630V_10PF; 1206-CAP
D1, D9, D11: RECTIFIER_800V_ACTIVE_SOD-123W; SOD-123W
D2: SCHOTTKY_SOD323_30VV; SOD-323
D10, D13: TVS_TPSMB_522.5; SMB(DO-214AA)
D12: ZENER_SMB(DO-214AA)_13V; SMB(DO-214AA)
IP+: TEST_POINT; 5015
IP-: TEST_POINT; 5015
IT+: TEST_POINT; 5015
IT-: TEST_POINT; 5015
J1: CONNECTOR-2_MICROFIT_PTH_VERTICAL_02_SINGLE_; MOLEX_MICROFIT_PTH_VERTICAL_02_SINGLE
L1: INDUCTOR_CDEEH13D90-102LC_1MH; CDEEH13D90
PACK_INP: TEST_POINT; 5015
PACK_ISO_DIAG: TEST_POINT; 5015
Q1: TRANSISTOR_N_MOS_2-7K1S_TK3P80E; DPAK(2-7K1S)
R1, R12: RESISTOR_0603_DNP; 0603-RES
R2, R3: RESISTOR_0603_330K; 0603-RES
R4: RESISTOR_0805_365K; 0805-RES
R5: RESISTOR_0603_20K; 0603-RES
R6: RESISTOR_0603_12.4K; 0603-RES
R7: RESISTOR_0603_12K; 0603-RES
R8: RESISTOR_0603_2.55K; 0603-RES
R9: RESISTOR_0603_1K; 0603-RES
R14: RESISTOR_0603_3.3; 0603-RES
R15: RESISTOR_0603_2.49K; 0603-RES
R18: RESISTOR_0603_21.5K; 0603-RES
R40: RESISTOR_0603_22.1K; 0603-RES
R50: RESISTOR_0603_2K; 0603-RES
R51: RESISTOR_0603_0.12; 0603-RES
R52, R53, R57, R58: RESISTOR_0805_HV365K; 0805-RES
R54, R59: RESISTOR_0805_HV1M; 0805-RES
R55, R60: RESISTOR_0603_HV3.3K; 0603-RES
R56, R61: RESISTOR_1206_HV4.99K; 1206-RES
TS+12V: TEST_POINT; 5015
TS-FUSED: TEST_POINT; 5015
TS/3: TEST_POINT; 5015
TS_INP: TEST_POINT; 5015
TS_ISO_DIAG: TEST_POINT; 5015
U1: OPAMP_1_CHANNEL_OPA991; SC-70-5
U2: LT8316; TSSOP-20(16)
U7, U8: AMC3330_AIRGAP; SOIC-16W-AIRGAP

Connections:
12VTS_A: 12VTS.2 (A), R12.1, R50.1
+5V: C31.1, C36.1, C44.1, C45.1, U7.12 (VDD), U8.12 (VDD); also elsewhere on the board
AIL+: J1.1, R1.2, R9.1, R12.2
BIAS: C33.1, D2.C, U2.9 (BIAS)
DCM: C54.2, U2.10 (DCM)
FB: R15.1, R18.2, U2.12 (FB)
G: R14.1, U2.19 (GATE)
GND: C31.2, C36.2, C37.2, C44.2, C45.2, C46.2, U7.9 (GND), U7.15 (DCDC_GND), U8.9 (GND), U8.15 (DCDC_GND); also elsewhere on the board
INTVCC: C32.1, U2.8 (INTVCC), U2.17 (EN/UVLO)
IP+: IP+.1, U8.11 (OUTP); also elsewhere on the board
IP-: IP-.1, U8.10 (OUTN); also elsewhere on the board
IT+: IT+.1, U7.11 (OUTP); also elsewhere on the board
IT-: IT-.1, U7.10 (OUTN); also elsewhere on the board
unnamed: Q1.1 (G), R14.2
unnamed: D2.A, D9.C, R15.2
unnamed: R2.1, R3.2, TS/3.1
unnamed: R2.2, R4.1
unnamed: R6.2, R7.1
unnamed: R56.2, R61.1
unnamed: C54.1, R61.2
unnamed: C37.1, U7.13 (LDO_OUT), U7.16 (DCDC_IN)
unnamed: C30.1, R40.1
unnamed: C46.1, U8.13 (LDO_OUT), U8.16 (DCDC_IN)
unnamed: R52.2, R53.1
unnamed: R53.2, R54.1
unnamed: R57.2, R58.1
unnamed: R58.2, R59.1
PACK+FUSED: R59.2; also elsewhere on the board
PACK_DCDC_OUT: C49.1, C50.1, C51.2, U8.1 (DCDC_OUT), U8.3 (HLDO_IN)
PACK_HLDO_OUT: C47.1, C48.1, U8.5 (HLDO_OUT)
PACK_INP: C52.1, PACK_INP.1, R57.1, R60.2, U8.6 (INP)
PACK_ISO_DIAG: PACK_ISO_DIAG.1, U8.14 (DIAG)
PACK_OPA_OUT: R9.2, U1.4 (VOUT)
SENSE: Q1.3 (S), R51.2, U2.18 (SENSE)
SS: C10.1, U2.14 (IREG)
SW: C10.2, C30.2, C32.2, C33.2, D11.C, L1.1, R18.1, R51.1, U2.15 (GND), U2.16 (SMODE), U2.20 (GND), U2.THERMAL
TS+12V: C3.1, C4.1, C5.1, C6.1, C7.1, C9.1, D9.A, D12.C, L1.2, R1.1, R7.2, R50.2, TS+12V.1, U1.5 (VDD)
TS+FUSED: D1.A, D10.C, R4.2; also elsewhere on the board
TS+UNFUSED: R54.2; also elsewhere on the board
TS-FUSED: 12VTS.1 (C), C1.2, C2.2, C3.2, C4.2, C5.2, C6.2, C7.2, C8.2, C9.2, C35.2, C38.2, C39.2, C40.2, C41.2, C42.1, C43.2, C47.2, C48.2, C49.2, C50.2, C51.1, C52.2, D10.A, D11.A, D12.A, D13.A, J1.2, R5.1, R8.1, R55.1, R60.1, TS-FUSED.1, U1.2 (GND), U7.2 (DCDC_HGND), U7.7 (INN), U7.8 (HGND), U8.2 (DCDC_HGND), U8.7 (INN), U8.8 (HGND); also elsewhere on the board
TS_DCDC_OUT: C40.1, C41.1, C42.2, U7.1 (DCDC_OUT), U7.3 (HLDO_IN)
TS_HLDO_OUT: C38.1, C39.1, U7.5 (HLDO_OUT)
TS_INP: C43.1, R52.1, R55.2, TS_INP.1, U7.6 (INP)
TS_ISO_DIAG: TS_ISO_DIAG.1, U7.14 (DIAG)
U1+: C2.1, R3.1, R5.2, U1.1 (VIN+)
U1-: C1.1, R6.1, R8.2, U1.3 (VIN-)
VC: R40.2, U2.13 (VC)
VIN: C8.1, C35.1, D1.C, D13.C, Q1.2 (D), R56.1, U2.1 (VIN), U2.2 (VIN), U2.3 (VIN)

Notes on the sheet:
AIL Driver
Precharge Isolation
Divider Ratio: 0.001904 Max Input: 533V * 0.001904 = 1.01477V < 1.25V Min Input: 377V * 0.001904 = 0.71776V < 1.25V
Nominal Gain: 2 Max Output = Max Input * 2 = 2.02954V < 2.5V Min Output = Min Input * 2 = 1.43553V < 2.5V
U1+ Divider Ratio: 0.019139 U1- Divider Ratio: 0.09462 U1- Input: 12V * 0.09462 = 1.1354V AIL Powered: 1.1354V / 0.019139 = 59.3258V < 60V ***R2~R4 are incorrectly sized, see sheet 3 for possible fixes

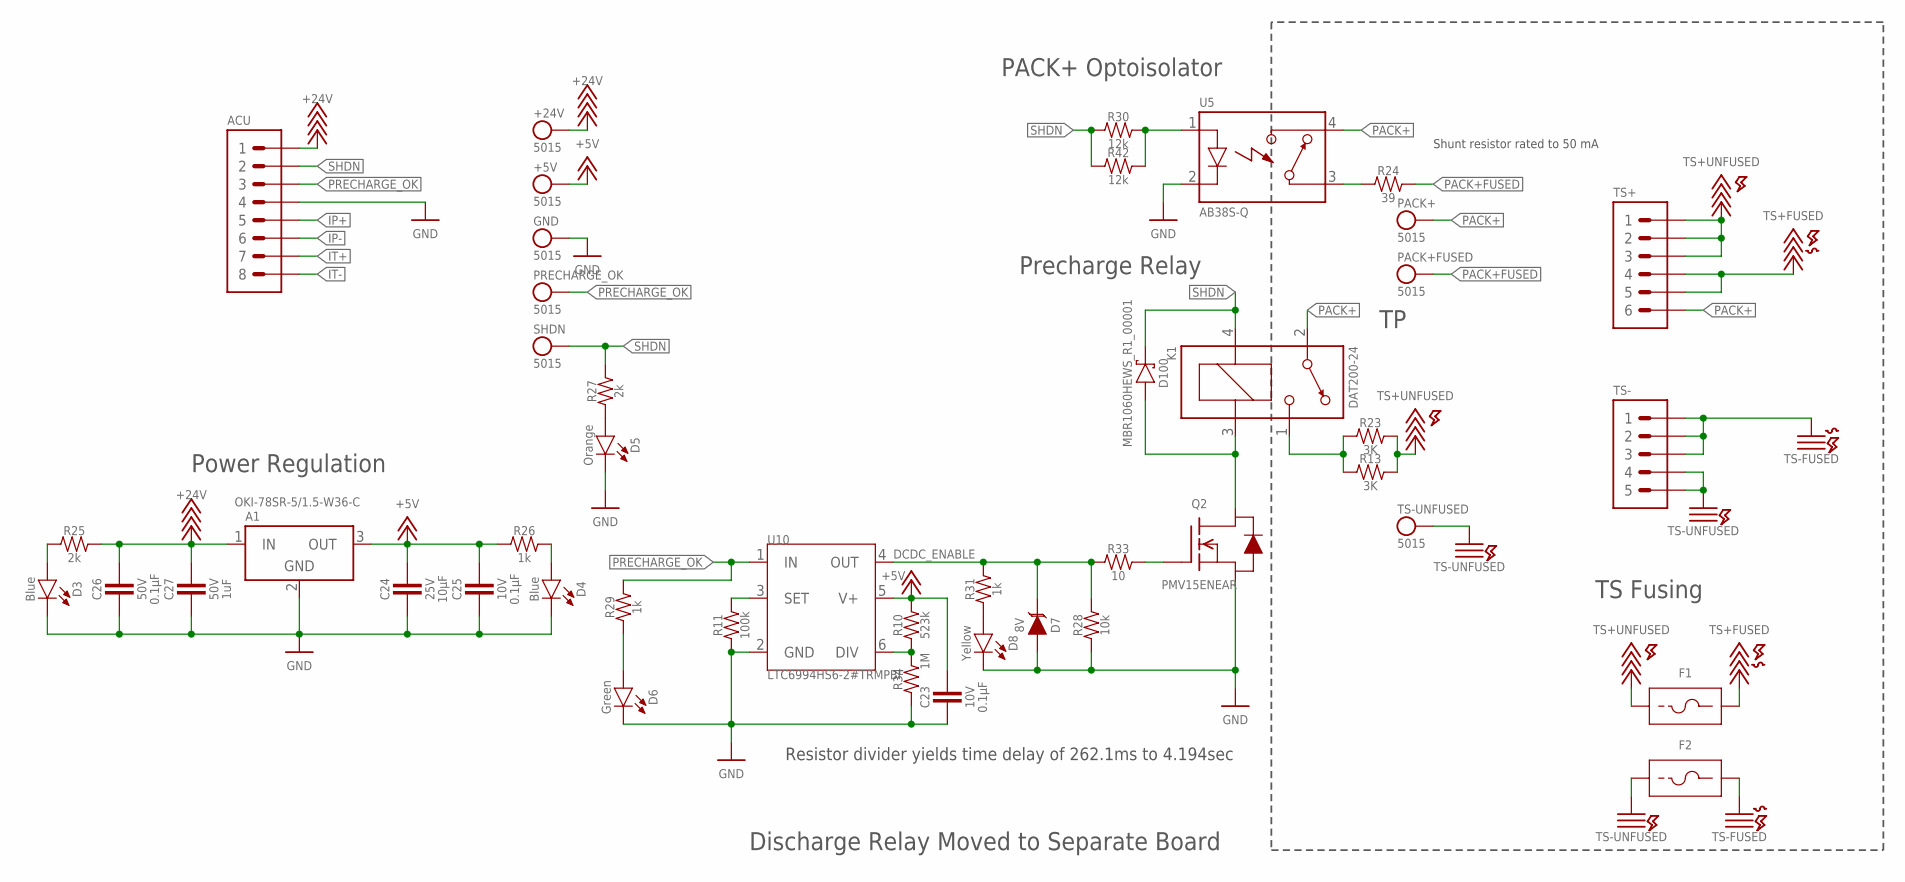
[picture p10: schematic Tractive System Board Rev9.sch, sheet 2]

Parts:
+5V, +24V: TEST_POINT; 5015
A1: VOLTAGE_REGULATOR_MODULE_OKI-78SR_5V; OKI-78SR
ACU: CONNECTOR-8_μF_T_V_BLACK; MOLEX_MICROFIT_PTH_VERTICAL_08_DUAL
C23, C25: CAPACITOR_0603_10V_0.1UF; 0603-CAP
C24: CAPACITOR_0603_25V_10UF; 0603-CAP
C26: CAPACITOR_0603_50V_0.1UF; 0603-CAP
C27: CAPACITOR_0603_50V_1UF; 0603-CAP
D3, D4: LED_0603_BLUE; 0603-LED
D5: LED_0603_ORANGE; 0603-LED
D6: LED_0603_GREEN; 0603-LED
D7: TVS__8V; SOT-23
D8: LED_0603_YELLOW; 0603-LED
D100: SCHOTTKY_SOD323_60V; SOD-323
F1, F2: FUSE_HOLDER_122; 122
GND: TEST_POINT; 5015
K1: RELAY_SPST_NO_D_200W_24; D
PACK+: TEST_POINT; 5015
PACK+FUSED: TEST_POINT; 5015
PRECHARGE_OK: TEST_POINT; 5015
Q2: TRANSISTOR_N_MOS__PMV15ENEA; SOT-23
R10: RESISTOR_0805_523K; 0805-RES
R11: RESISTOR_0603_100K_0.1%; 0603-RES
R13: RESISTOR_B20-SHORTENED_1.5K; B20-SHORTENED; MPN B20J3K0E
R23: 3K; B20-SHORTENED; MPN B20J3K0E
R24: RESISTOR_0603_39; 0603-RES
R25, R27: RESISTOR_0603_2K; 0603-RES
R26, R29, R31: RESISTOR_0603_1K; 0603-RES
R28: RESISTOR_0603_10K; 0603-RES
R30, R42: RESISTOR_0603_12K; 0603-RES
R33: RESISTOR_0603_10; 0603-RES
R34: RESISTOR_0805_1M; 0805-RES
SHDN: TEST_POINT; 5015
TS+: CONNECTOR-6_μF_S_V_TSB_; MOLEX_MICROFIT_PTH_VERTICAL_08_SINGLE_SPACED_MODIFIED
TS-: CONNECTOR-5_MICRO_V6S_; MOLEX_MICROFIT_PTH_VERTICAL_06_SINGLE_SPACED
TS-UNFUSED: TEST_POINT; 5015
U5: RELAY_SOLIDSTATE_NO_AB38S-Q-AIRGAP; SOP-04-AIRGAP
U10: LTC6994-2; SOT-23-6

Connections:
+5V: +5V.1, A1.3 (OUT), C23.1, C24.1, C25.1, R10.2, R26.1, U10.5 (V+); also elsewhere on the board
+24V: +24V.1, A1.1 (IN), ACU.1, C26.1, C27.1, R25.2
DCDC_ENABLE: D7.3 (C), R28.2, R31.2, R33.1, U10.4 (OUT)
GND: A1.2 (GND), ACU.4, C23.2, C24.2, C25.2, C26.2, C27.2, D3.1 (C), D4.1 (C), D5.1 (C), D6.1 (C), D7.1 (A), D8.1 (C), GND.1, Q2.2 (S), R11.1, R28.1, R34.1, U5.2 (CONTROL-), U10.2 (GND); also elsewhere on the board
IP+: ACU.5; also elsewhere on the board
IP-: ACU.6; also elsewhere on the board
IT+: ACU.7; also elsewhere on the board
IT-: ACU.8; also elsewhere on the board
unnamed: D5.2 (A), R27.1
unnamed: Q2.1 (G), R33.2
unnamed: R11.2, U10.3 (SET)
unnamed: R10.1, R34.2, U10.6 (DIV)
unnamed: D6.2 (A), R29.1
unnamed: D8.2 (A), R31.1
unnamed: D3.2 (A), R25.1
unnamed: D4.2 (A), R26.2
unnamed: D100.A, K1.3 (COIL-), Q2.3 (D)
unnamed: K1.1 (CONTACT2), R13.1, R23.1
unnamed: R30.2, R42.2, U5.1 (CONTROL+)
unnamed: R24.1, U5.3 (CONTACT1)
PACK+: K1.2 (CONTACT1), PACK+.1, TS+.6, U5.4 (CONTACT2)
PACK+FUSED: PACK+FUSED.1, R24.2; also elsewhere on the board
PRECHARGE_OK: ACU.3, PRECHARGE_OK.1, R29.2, U10.1 (IN)
SHDN: ACU.2, D100.C, K1.4 (COIL+), R27.2, R30.1, R42.1, SHDN.1
TS+FUSED: F1.3 (2), F1.4 (2), TS+.4, TS+.5; also elsewhere on the board
TS+UNFUSED: F1.1, F1.2 (1), R13.2, R23.2, TS+.1, TS+.2, TS+.3; also elsewhere on the board
TS-FUSED: F2.3 (2), F2.4 (2), TS-.1, TS-.2, TS-.3; also elsewhere on the board
TS-UNFUSED: F2.1, F2.2 (1), TS-.4, TS-.5, TS-UNFUSED.1

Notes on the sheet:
PACK+ Optoisolator
Precharge Relay
Discharge Relay Moved to Separate Board
TS Fusing
Power Regulation
Shunt resistor rated to 50 mA
Resistor divider yields time delay of 262.1ms to 4.194sec

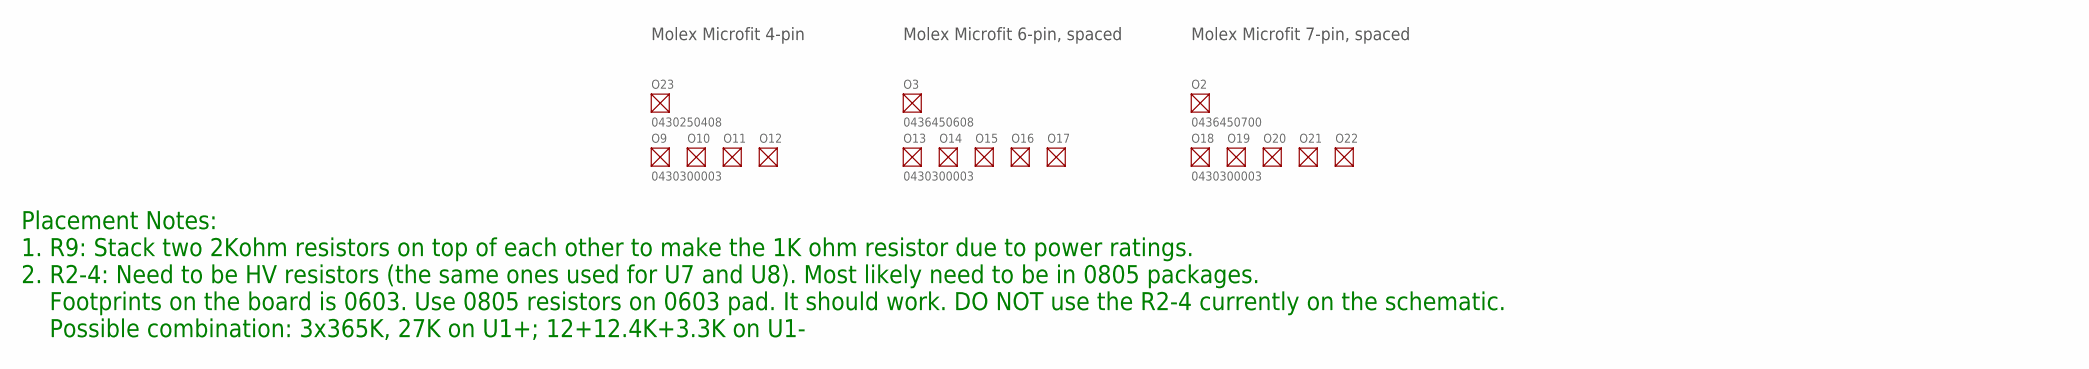
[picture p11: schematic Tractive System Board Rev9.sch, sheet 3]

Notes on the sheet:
Molex Microfit 4-pin
Molex Microfit 6-pin, spaced
Molex Microfit 7-pin, spaced
Placement Notes: 1. R9: Stack two 2Kohm resistors on top of each other to make the 1K ohm resistor due to power ratings. 2. R2-4: Need to be HV resistors (the same ones used for U7 and U8). Most likely need to be in 0805 packages. Footprints on the board is 0603. Use 0805 resistors on 0603 pad. It 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

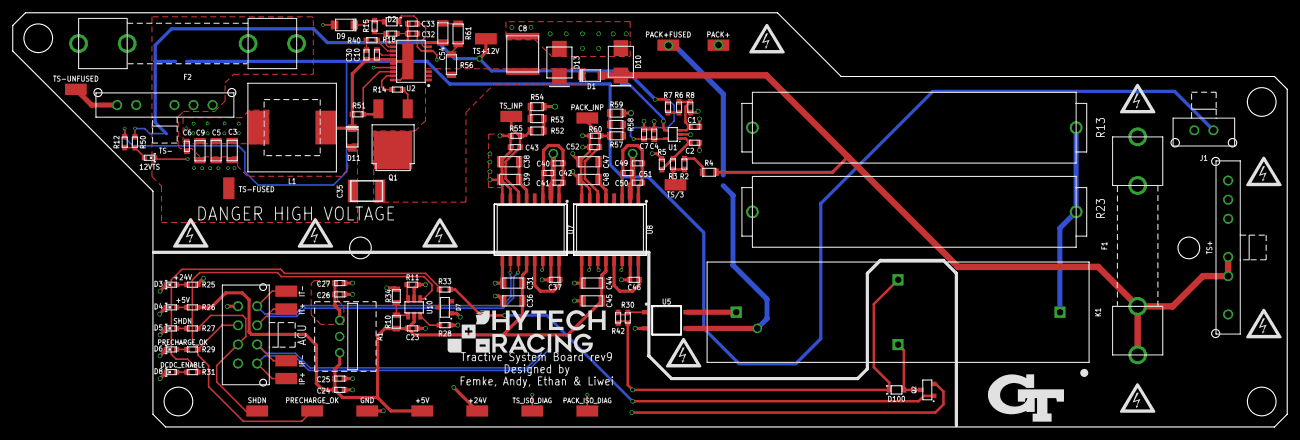
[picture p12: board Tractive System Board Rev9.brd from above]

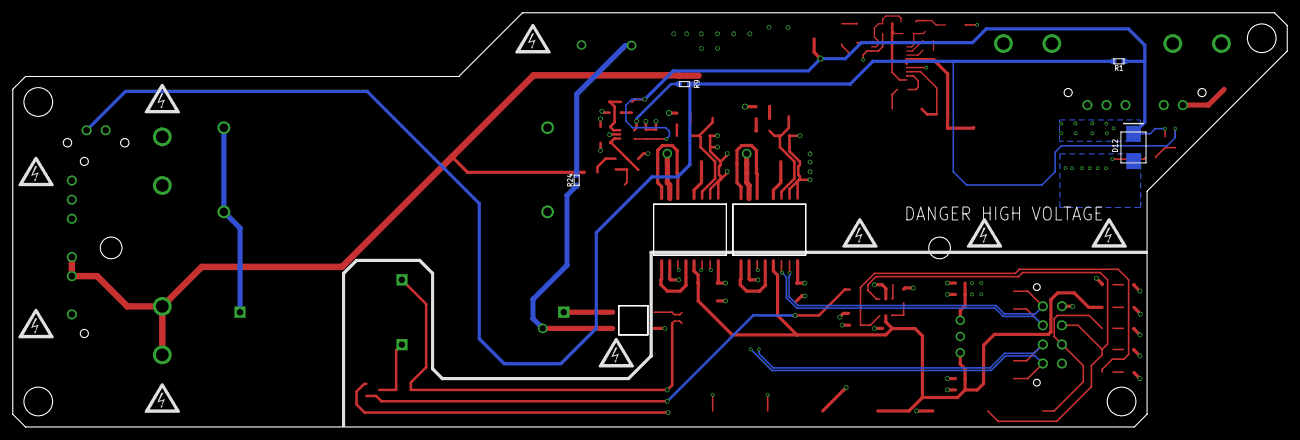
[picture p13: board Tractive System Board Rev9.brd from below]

Board: 4 copper layers, 200.0 x 65.0 mm, 157 parts (13 on the bottom side), 66 nets.

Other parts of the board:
$$U$1, $$U$4, $$U$6, $$U$8, $$U$104, $$U$105, $$U$106, $$U$107: HV_MEDIUM
U$2, U$6, U$17, U$22: MOUNTING_M4
U$7: DANGER_HIGH_VOLTAGE
U$8, U$9, U$13, U$14, U$15, U$16, U$100, U$101, U$102, U$103: HV_MEDIUM
U$10: LOGO_HYTECH_MEDIUM
U$11, U$12: MOUNTING_M3
U$18: LOGO_GT_MEDIUM

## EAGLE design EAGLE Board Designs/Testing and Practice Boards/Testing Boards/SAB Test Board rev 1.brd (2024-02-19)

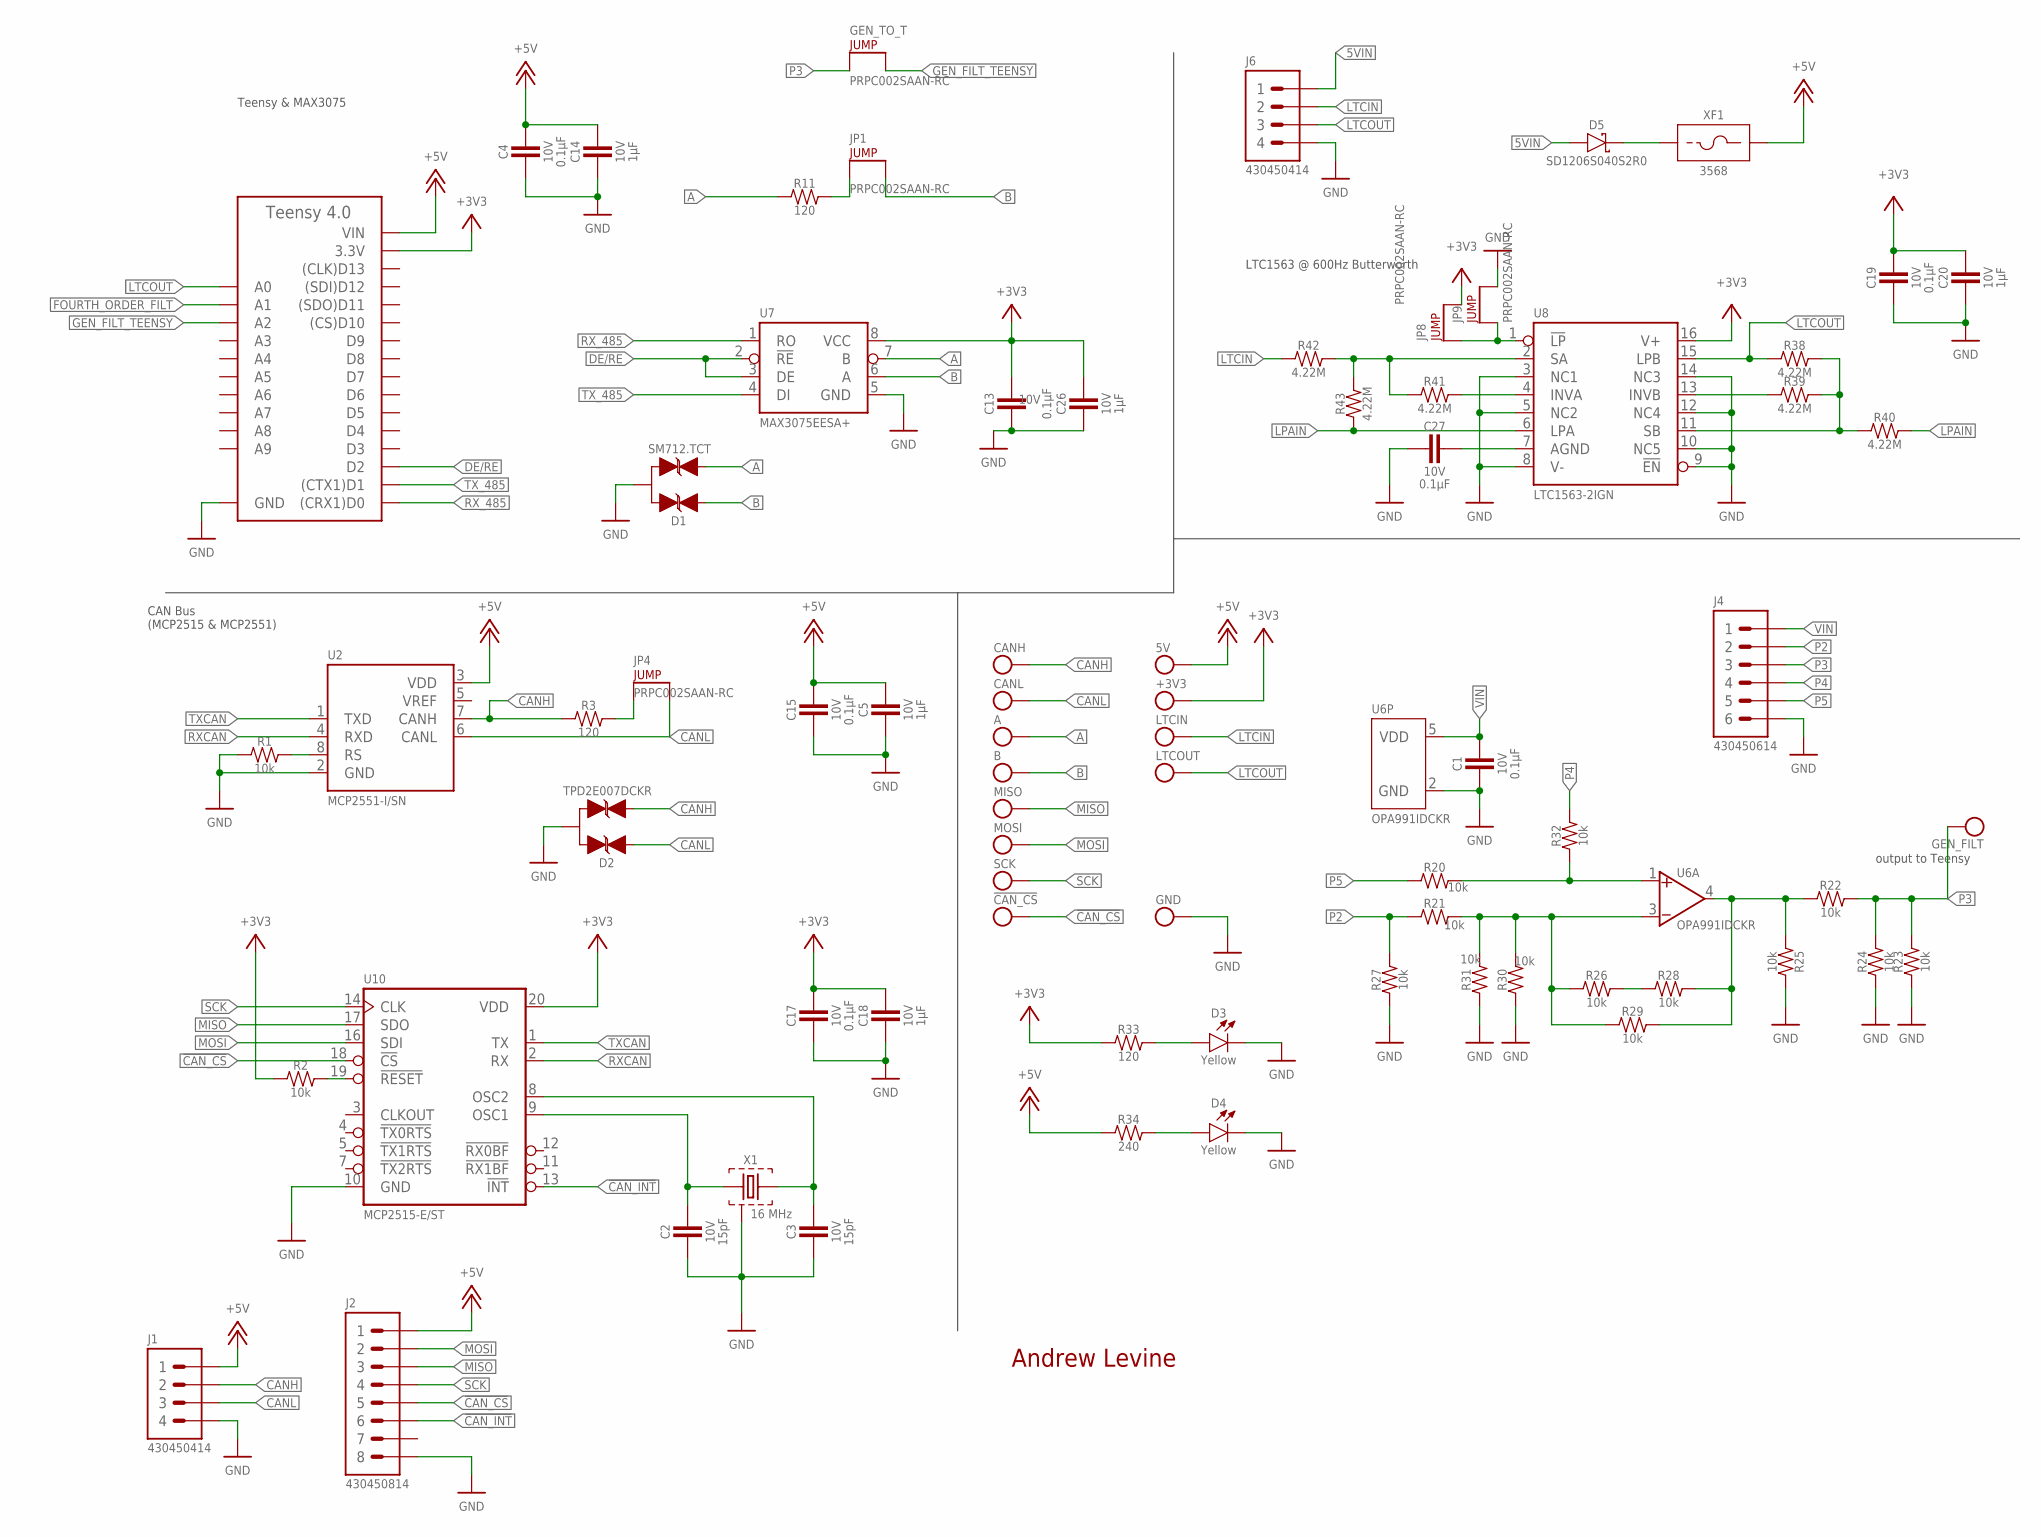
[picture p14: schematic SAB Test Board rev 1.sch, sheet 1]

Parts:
5V: TEST_POINT; 5015
!CAN_CS: TEST_POINT; 5015
+3V3: TEST_POINT; 5015
A: TEST_POINT; 5015
A1: TEENSY_4.0TH; TEENSY_SHORT
B: TEST_POINT; 5015
C1, C4, C13, C15, C17, C19, C27: CAPACITOR_0603_10V_0.1UF; 0603-CAP
C2, C3: CAPACITOR_0603_10V_15PF; 0603-CAP
C5, C14, C18, C20, C26: CAPACITOR_0603_10V_1UF; 0603-CAP
CANH: TEST_POINT; 5015
CANL: TEST_POINT; 5015
D1: TVS_BIDIRECTIONAL_DUALRS422; SOT-23
D2: TVS_BIDIRECTIONAL_DUAL; SC-70-3
D3, D4: LED_0603_YELLOW; 0603-LED
D5: SCHOTTKY_1206_40V; 1206-DIODE
GEN_FILT: TEST_POINT; 5015
GEN_TO_T: JUMPER__1X02; 1X02
GND: TEST_POINT; 5015
J1, J6: CONNECTOR-4_μF_T_V_BLACK; MOLEX_MICROFIT_PTH_VERTICAL_04_DUAL
J2: CONNECTOR-8_μF_T_V_BLACK; MOLEX_MICROFIT_PTH_VERTICAL_08_DUAL
J4: CONNECTOR-6_μF_T_V_BLACK; MOLEX_MICROFIT_PTH_VERTICAL_06_DUAL
JP1, JP4, JP8, JP9: JUMPER__1X02; 1X02
LTCIN: TEST_POINT; 5015
LTCOUT: TEST_POINT; 5015
MISO: TEST_POINT; 5015
MOSI: TEST_POINT; 5015
R1, R2, R20, R21, R22, R23, R24, R25, R26, R27, R28, R29, R30, R31, R32: RESISTOR_0603_10K; 0603-RES
R3, R11, R33: RESISTOR_0603_120; 0603-RES
R34: RESISTOR_0603_240; 0603-RES
R38, R39, R40, R41, R42, R43: RESISTOR_0603_4.22M; 0603-RES
SCK: TEST_POINT; 5015
U2: MCP2551; SOIC-08(NARROW,0.15")
U6: OPAMP_1_CHANNEL_OPA991; SC-70-5
U7: MAX3075; SOIC-08(NARROW,0.15")
U8: LTC1563; SSOP-16
U10: MCP2515; TSSOP-20
X1: CRYSTAL_16MHZ; ECX-42
XF1: FUSE_HOLDER_MINIBLADEPTH; 3568

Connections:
5VIN: D5.1 (A), J6.1
!CAN_CS: !CAN_CS.1, J2.5, U10.18 (!CS)
!CAN_INT: J2.6, U10.13 (!INT)
+3V3: +3V3.1, A1.3.3V, C13.1, C17.1, C18.1, C19.1, C20.1, C26.1, JP8.2, R2.1, R33.1, U7.8 (VCC), U8.16 (V+), U10.20 (VDD); also elsewhere on the board
+5V: 5V.1, A1.VIN, C4.1, C5.1, C14.1, C15.1, J1.1, J2.1, R34.1, U2.3 (VDD), XF1.3 (2), XF1.4 (2); also elsewhere on the board
A: A.1, D1.2 (C2), R11.1, U7.7 (B)
B: B.1, D1.1 (C1), JP1.2, U7.6 (A)
CANH: CANH.1, D2.2 (C2), J1.2, R3.1, U2.7 (CANH)
CANL: CANL.1, D2.1 (C1), J1.3, JP4.2, U2.6 (CANL)
DE/RE: A1.D2, U7.2 (!RE), U7.3 (DE)
FOURTH_ORDER_FILT: A1.D15 (A1); also elsewhere on the board
GEN_FILT_TEENSY: A1.D16 (A2), GEN_TO_T.2
GND: A1.AGND/GND (GND), A1.GND, C1.2, C2.2, C3.2, C4.2, C5.2, C13.2, C14.2, C15.2, C17.2, C18.2, C19.2, C20.2, C26.2, C27.2, D1.3 (A), D2.3 (A), D3.1 (C), D4.1 (C), GND.1, J1.4, J2.8, J4.6, J6.4, JP9.2, R1.1, R23.1, R24.1, R25.2, R27.1, R30.1, R31.1, U2.2 (GND), U6.2 (GND), U7.5 (GND), U8.3 (NC1), U8.5 (NC2), U8.8 (V-), U8.9 (!EN), U8.10 (NC5), U8.12 (NC4), U8.14 (NC3), U10.10 (GND), X1.2 (GND), X1.4 (GND); also elsewhere on the board
LPAIN: R40.2, R43.1, U8.6 (LPA)
LTCIN: J6.2, LTCIN.1, R42.1
LTCOUT: A1.D14 (A0), J6.3, LTCOUT.1, R38.1, U8.15 (LPB)
MISO: J2.3, MISO.1, U10.17 (SDO)
MOSI: J2.2, MOSI.1, U10.16 (SDI)
unnamed: C2.1, U10.9 (OSC1), X1.1
unnamed: C3.1, U10.8 (OSC2), X1.3
unnamed: R1.2, U2.8 (RS)
unnamed: JP4.1, R3.2
unnamed: R2.2, U10.19 (!RESET)
unnamed: D5.2 (C), XF1.1, XF1.2 (1)
unnamed: JP1.1, R11.2
unnamed: R22.1, R25.1, R28.2, R29.2, U6.4 (VOUT)
unnamed: JP8.1, JP9.1, U8.1 (!LP)
unnamed: R20.2, R32.1, U6.1 (VIN+)
unnamed: D3.2 (A), R33.2
unnamed: D4.2 (A), R34.2
unnamed: R26.2, R28.1
unnamed: R21.2, R26.1, R29.1, R30.2, R31.2, U6.3 (VIN-)
unnamed: C27.1, U8.7 (AGND)
unnamed: R39.1, U8.13 (INVB)
unnamed: R38.2, R39.2, R40.1, U8.11 (SB)
unnamed: R41.2, U8.4 (INVA)
unnamed: R41.1, R42.2, R43.2, U8.2 (SA)
P2: J4.2, R21.1, R27.2
P3: GEN_FILT.1, GEN_TO_T.1, J4.3, R22.2, R23.2, R24.2
P4: J4.4, R32.2
P5: J4.5, R20.1
RXCAN: U2.4 (RXD), U10.2 (RX)
RX_485: A1.D0 ((CRX1)D0), U7.1 (RO)
SCK: J2.4, SCK.1, U10.14 (CLK)
TXCAN: U2.1 (TXD), U10.1 (TX)
TX_485: A1.D1 ((CTX1)D1), U7.4 (DI)
VIN: C1.1, J4.1, U6.5 (VDD)
VREF: U2.5 (VREF)

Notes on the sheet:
Andrew Levine
CAN Bus (MCP2515 & MCP2551)
Teensy & MAX3075
LTC1563 @ 600Hz Butterworth
output to Teensy

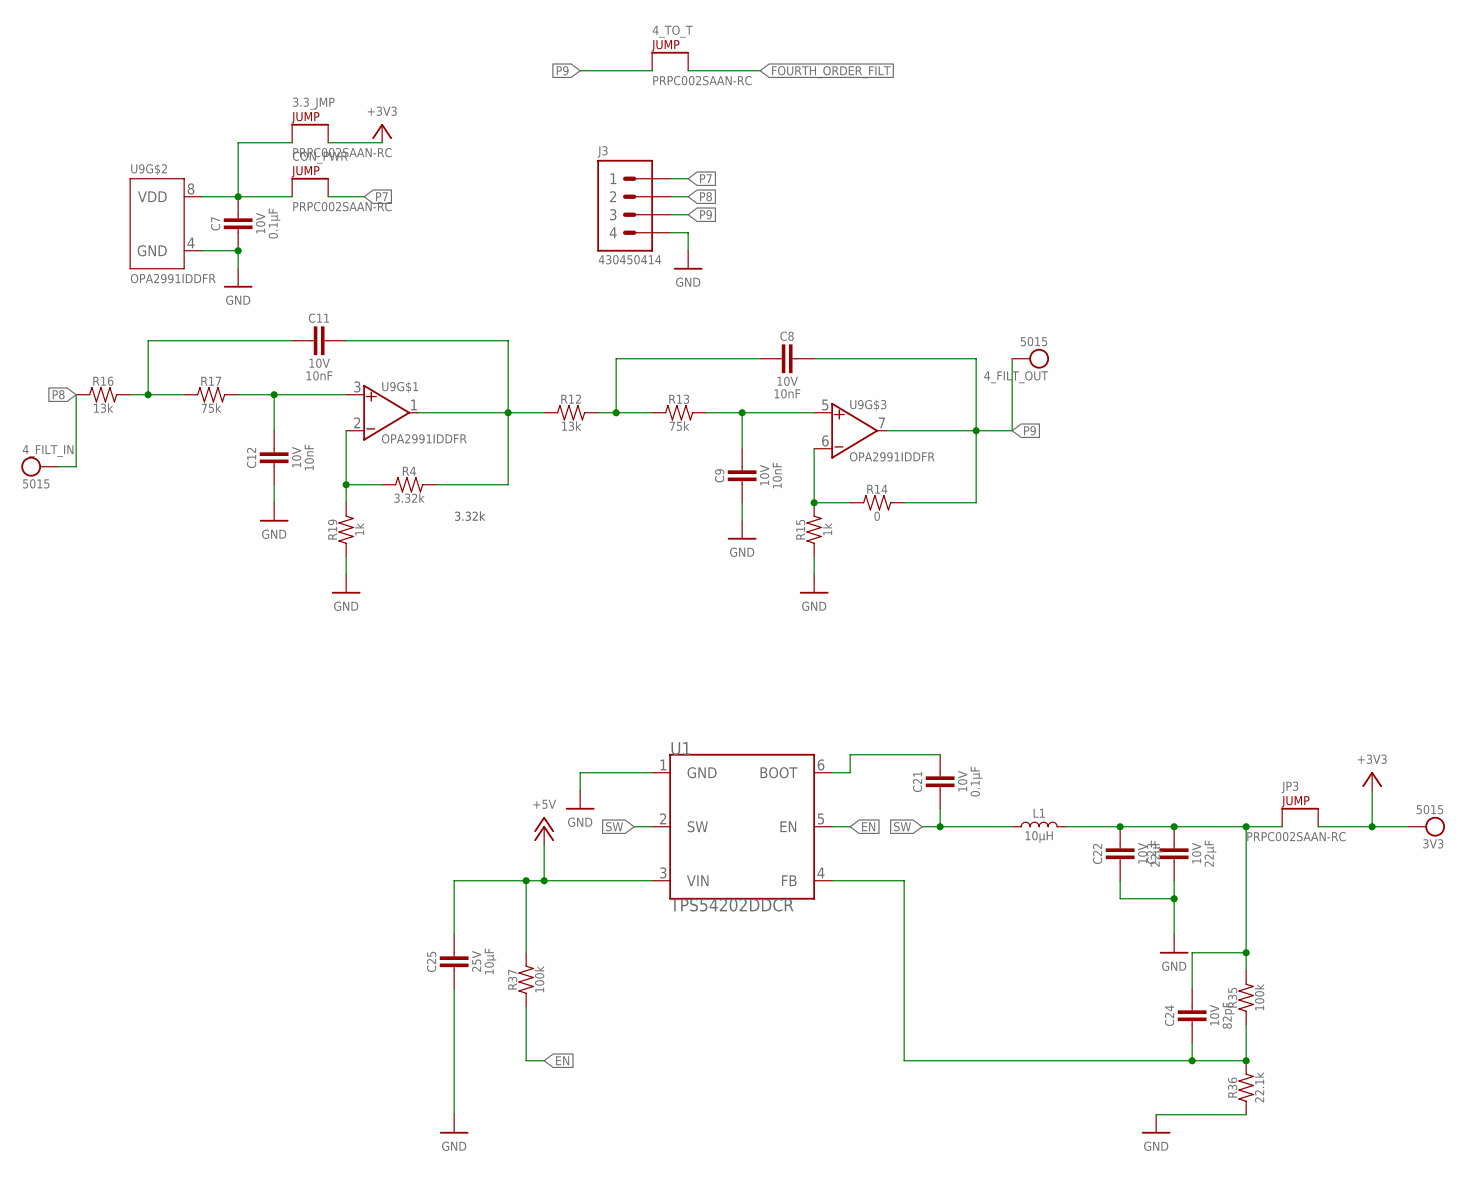
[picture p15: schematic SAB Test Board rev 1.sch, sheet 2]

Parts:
3.3_JMP, 4_TO_T: JUMPER__1X02; 1X02
3V3, 4_FILT_IN, 4_FILT_OUT: TEST_POINT; 5015
C7, C21: CAPACITOR_0603_10V_0.1UF; 0603-CAP
C8, C9, C11, C12: CAPACITOR_0603_10V_10NF; 0603-CAP
C22, C23: CAPACITOR_0603_10V_22UF; 0603-CAP
C24: CAPACITOR_0603_10V_82PF; 0603-CAP
C25: CAPACITOR_0603_25V_10UF; 0603-CAP
CON_PWR: JUMPER__1X02; 1X02
J3: CONNECTOR-4_μF_T_V_BLACK; MOLEX_MICROFIT_PTH_VERTICAL_04_DUAL
JP3: JUMPER__1X02; 1X02
L1: INDUCTOR_PA4334_10UH; PA4334
R4: RESISTOR_0603_3.32K; 0603-RES
R12, R16: RESISTOR_0603_13K; 0603-RES
R13, R17: RESISTOR_0603_75K; 0603-RES
R14: RESISTOR_0603_0; 0603-RES
R15, R19: RESISTOR_0603_1K; 0603-RES
R35, R37: RESISTOR_0603_100K; 0603-RES
R36: RESISTOR_0603_22.1K; 0603-RES
U1: TPS54202DDCR; SOT-23-6
U9: OPAMP_2_CHANNEL_OPA_2991; SOT-23-8

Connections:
+3V3: 3.3_JMP.2, 3V3.1, JP3.2; also elsewhere on the board
+5V: C25.1, R37.2, U1.3 (VIN); also elsewhere on the board
EN: R37.1, U1.5 (EN)
FOURTH_ORDER_FILT: 4_TO_T.2; also elsewhere on the board
GND: C7.2, C9.2, C12.2, C22.2, C23.2, C25.2, J3.4, R15.1, R19.1, R36.1, U1.1 (GND), U9.4 (GND); also elsewhere on the board
unnamed: C9.1, R13.2, U9.5 (VIN+)
unnamed: C8.2, R12.2, R13.1
unnamed: R14.1, R15.2, U9.6 (VIN-)
unnamed: C21.1, U1.6 (BOOT)
unnamed: C12.1, R17.2, U9.3 (VIN+)
unnamed: C11.2, R16.2, R17.1
unnamed: C11.1, R4.2, R12.1, U9.1 (VOUT)
unnamed: R4.1, R19.2, U9.2 (VIN-)
unnamed: C24.2, R35.1, R36.2, U1.4 (FB)
unnamed: C22.1, C23.1, C24.1, JP3.1, L1.2, R35.2
unnamed: 3.3_JMP.1, C7.1, CON_PWR.1, U9.8 (VDD)
P7: CON_PWR.2, J3.1
P8: 4_FILT_IN.1, J3.2, R16.1
P9: 4_FILT_OUT.1, 4_TO_T.1, C8.1, J3.3, R14.2, U9.7 (VOUT)
SW: C21.2, L1.1, U1.2 (SW)

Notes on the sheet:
3.32k

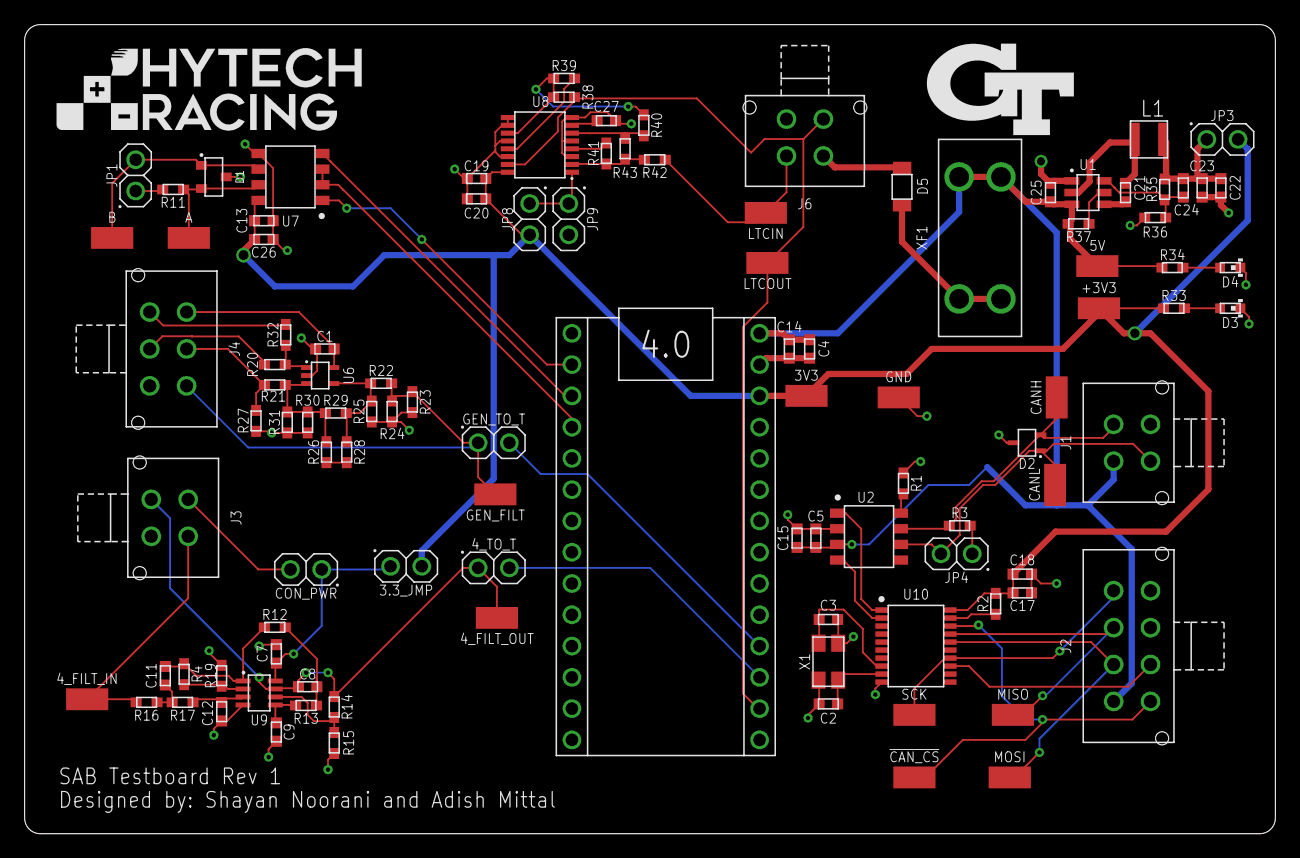
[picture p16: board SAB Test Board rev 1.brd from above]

Board: 2 copper layers, 101.6 x 65.7 mm, 109 parts (0 on the bottom side), 63 nets.

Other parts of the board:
U$1: LOGO_HYTECH_MEDIUM
U$3: LOGO_GT_MEDIUM

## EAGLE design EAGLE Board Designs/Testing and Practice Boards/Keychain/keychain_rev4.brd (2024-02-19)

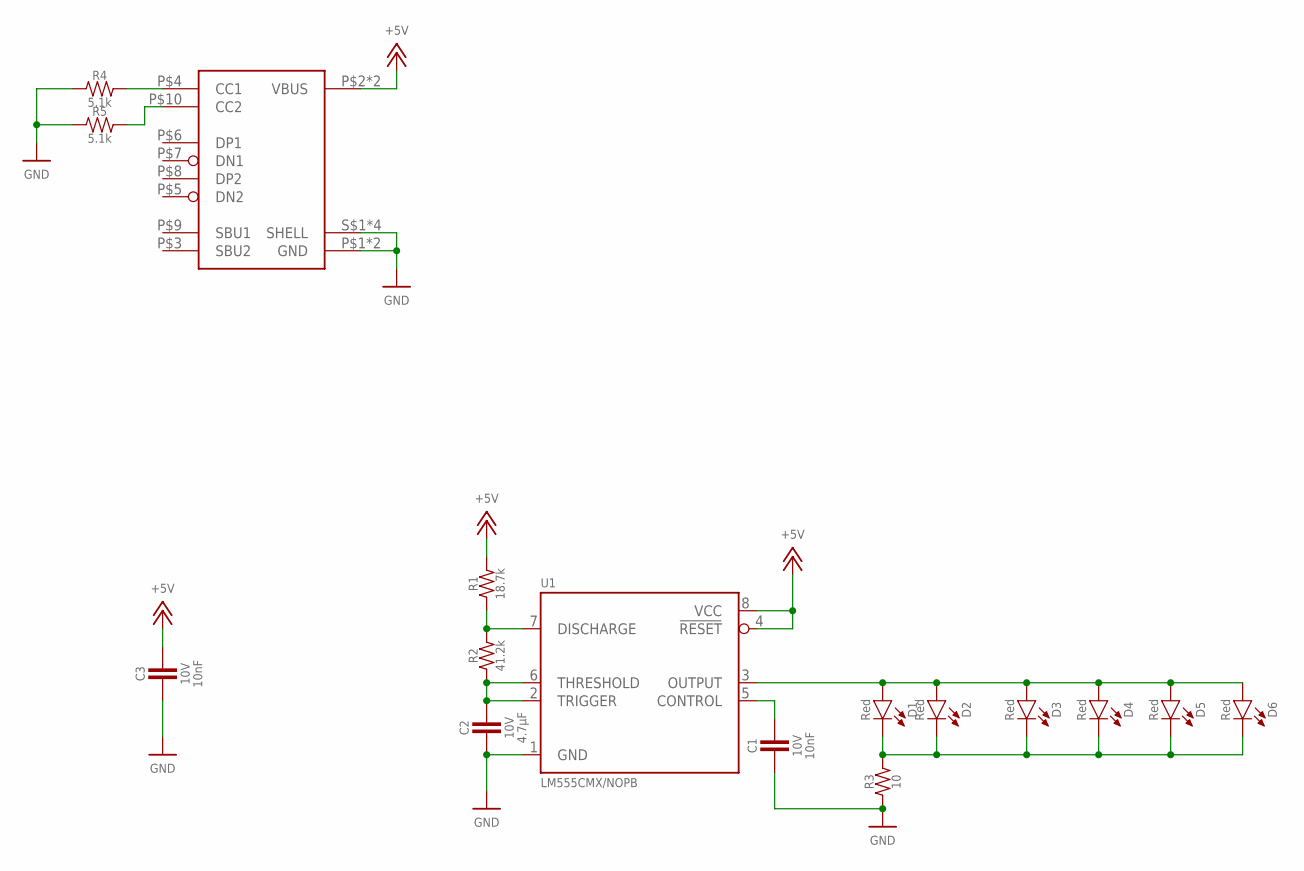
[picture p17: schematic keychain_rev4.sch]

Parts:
C1, C3: CAPACITOR_0603_10V_10NF; 0603-CAP
C2: CAPACITOR_0603_10V_4.7UF; 0603-CAP
D1, D2, D3, D4, D5, D6: LED_0603_RED; 0603-LED
J1: USB4110
R1: RESISTOR_0603_18.7K; 0603-RES
R2: RESISTOR_0603_41.2K; 0603-RES
R3: RESISTOR_0603_10; 0603-RES
R4, R5: RESISTOR_0603_5.1K; 0603-RES
U1: LM555; SOIC-08(NARROW,0.15")

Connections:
+5V: C3.1, J1.P$2 (VBUS), J1.P$11 (VBUS), R1.2, U1.4 (!RESET), U1.8 (VCC)
GND: C1.2, C2.2, C3.2, J1.P$1 (GND), J1.P$12 (GND), J1.S$1 (SHELL), J1.S$2 (SHELL), J1.S$3 (SHELL), J1.S$4 (SHELL), R3.1, R4.1, R5.1, U1.1 (GND)
unnamed: C1.1, U1.5 (CONTROL)
unnamed: D1.2 (A), D2.2 (A), D3.2 (A), D4.2 (A), D5.2 (A), D6.2 (A), U1.3 (OUTPUT)
unnamed: D1.1 (C), D2.1 (C), D3.1 (C), D4.1 (C), D5.1 (C), D6.1 (C), R3.2
unnamed: J1.P$4 (CC1), R4.2
unnamed: J1.P$10 (CC2), R5.2
unnamed: C2.1, R2.1, U1.2 (TRIGGER), U1.6 (THRESHOLD)
unnamed: R1.1, R2.2, U1.7 (DISCHARGE)

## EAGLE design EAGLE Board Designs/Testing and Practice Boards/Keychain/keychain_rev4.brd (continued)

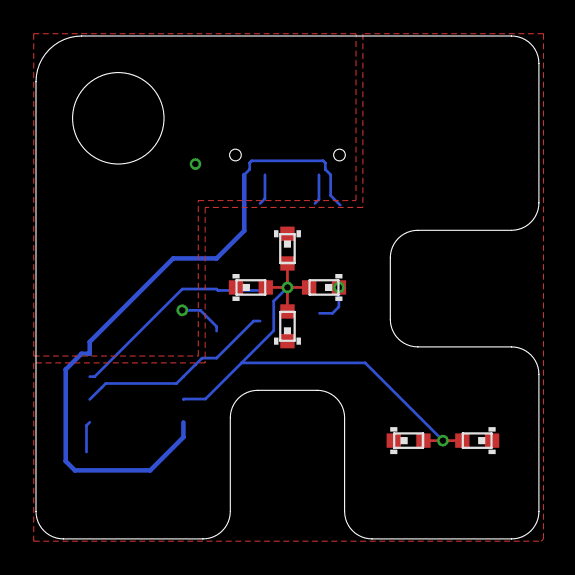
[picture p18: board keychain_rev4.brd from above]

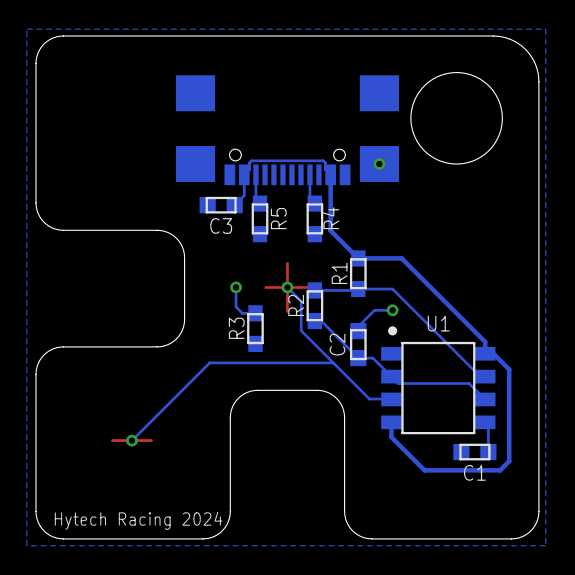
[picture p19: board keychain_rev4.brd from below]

Board: 2 copper layers, 27.9 x 27.9 mm, 16 parts (10 on the bottom side), 9 nets.

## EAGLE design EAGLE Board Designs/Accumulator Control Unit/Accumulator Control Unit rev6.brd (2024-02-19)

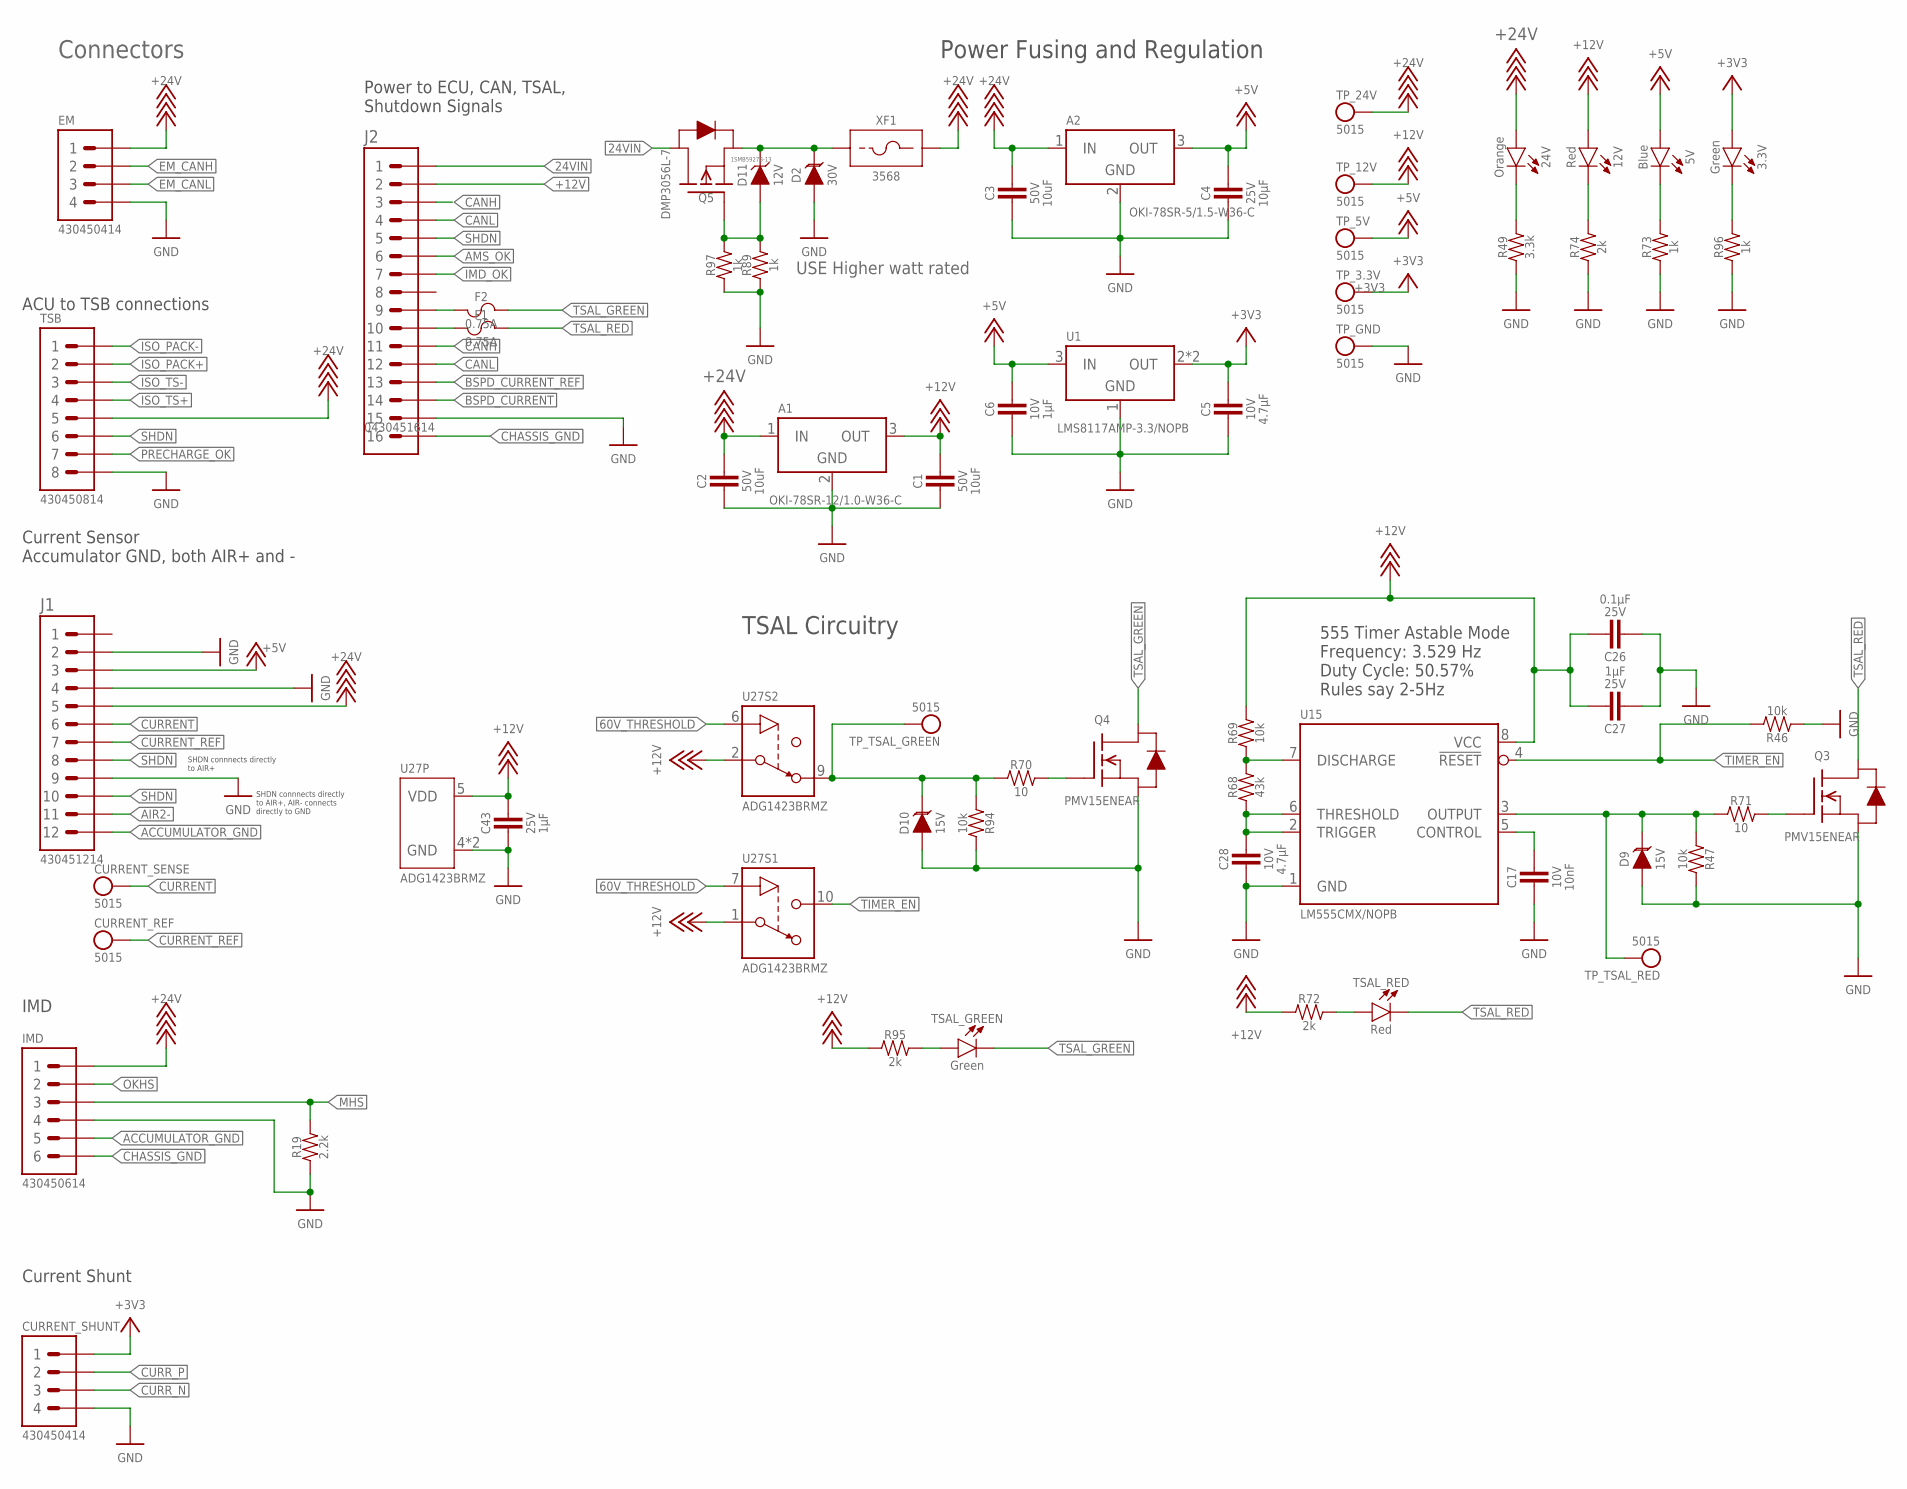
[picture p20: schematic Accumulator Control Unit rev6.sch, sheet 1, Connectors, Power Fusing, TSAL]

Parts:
3.3V: LED_0603_GREEN; 0603-LED
5V: LED_0603_BLUE; 0603-LED
12V: LED_0603_RED; 0603-LED
24V: LED_0603_ORANGE; 0603-LED
A1: VOLTAGE_REGULATOR_MODULE_OKI-78SR_12V; OKI-78SR
A2: VOLTAGE_REGULATOR_MODULE_OKI-78SR_5V; OKI-78SR
C1, C2, C3: CAPACITOR_0805_50V_10UF; 0805-CAP
C4: CAPACITOR_0603_25V_10UF; 0603-CAP
C5, C28: CAPACITOR_0603_10V_4.7UF; 0603-CAP
C6: CAPACITOR_0603_10V_1UF; 0603-CAP
C17: CAPACITOR_0603_10V_10NF; 0603-CAP
C26: CAPACITOR_0603_25V_0.1UF; 0603-CAP
C27, C43: CAPACITOR_0603_25V_1UF; 0603-CAP
CURRENT_REF: TEST_POINT; MICRO_MINIATURE
CURRENT_SENSE: TEST_POINT; MICRO_MINIATURE
CURRENT_SHUNT: CONNECTOR-4_μF_T_V_BLACK; MOLEX_MICROFIT_PTH_VERTICAL_04_DUAL
D2: TVS_DO-214AA_30V; DO-214AA
D9, D10: TVS__15V; SOT-23
D11: ZENER_1.5SMBJ_12V; 1.5SMBJ
EM: CONNECTOR-4_μF_T_V_BLACK; MOLEX_MICROFIT_PTH_VERTICAL_04_DUAL
F1, F2: FUSE_0603_.75A; 0603-FUSE
IMD: CONNECTOR-6_μF_T_V_BLACK; MOLEX_MICROFIT_PTH_VERTICAL_06_DUAL
J1: CONNECTOR-12_MF_T_V_; MOLEX_MICROFIT_PTH_VERTICAL_12_DUAL
J2: CONNECTOR-16_MF_T_V_; MOLEX_MICROFIT_PTH_VERTICAL_16_DUAL
Q3, Q4: TRANSISTOR_N_MOS__PMV15ENEA; SOT-23
Q5: TRANSISTOR_P_MOS_SOT-23_DMP3056L-7; SOT-23
R19: RESISTOR_0603_2.2K; 0603-RES
R46, R47, R69, R94: RESISTOR_0603_10K; 0603-RES
R49: RESISTOR_0603_3.3K; 0603-RES
R68: RESISTOR_0603_43K; 0603-RES
R70, R71: RESISTOR_0603_10; 0603-RES
R72, R74, R95: RESISTOR_0603_2K; 0603-RES
R73, R89, R96, R97: RESISTOR_0603_1K; 0603-RES
TP_3.3V, TP_5V, TP_12V, TP_24V: TEST_POINT; 5015
TP_GND: TEST_POINT; 5015
TP_TSAL_GREEN: TEST_POINT; MICRO_MINIATURE
TP_TSAL_RED: TEST_POINT; MICRO_MINIATURE
TSAL_GREEN: LED_0603_GREEN; 0603-LED
TSAL_RED: LED_0603_RED; 0603-LED
TSB: CONNECTOR-8_μF_T_V_BLACK; MOLEX_MICROFIT_PTH_VERTICAL_08_DUAL
U1: VOLTAGE_REGULATOR_SOT-223_3.3V; SOT-223
U15: LM555; SOIC-08(NARROW,0.15")
U27: ADG1423; MSOP-10
XF1: FUSE_HOLDER_MINIBLADEPTH; 3568

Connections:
24VIN: J2.1, Q5.3 (D)
60V_THRESHOLD: U27.6 (IN), U27.7 (IN); also elsewhere on the board
+3V3: 3.3V.2 (A), C5.1, CURRENT_SHUNT.1, TP_3.3V.1, U1.2 (OUT), U1.4 (OUT); also elsewhere on the board
+5V: 5V.2 (A), A2.3 (OUT), C4.1, C6.1, J1.3, TP_5V.1, U1.3 (IN); also elsewhere on the board
+12V: 12V.2 (A), A1.3 (OUT), C1.1, C26.1, C27.1, C43.1, J2.2, R69.2, R72.1, R95.1, TP_12V.1, U15.8 (VCC), U27.1 (S), U27.2 (S), U27.5 (VDD); also elsewhere on the board
+24V: 24V.2 (A), A1.1 (IN), A2.1 (IN), C2.1, C3.1, EM.1, IMD.1, J1.5, TP_24V.1, TSB.5, XF1.3 (2), XF1.4 (2); also elsewhere on the board
ACCUMULATOR_GND: IMD.5, J1.12
AIR2-: J1.11; also elsewhere on the board
AMS_OK: J2.6; also elsewhere on the board
BSPD_CURRENT: J2.14; also elsewhere on the board
BSPD_CURRENT_REF: J2.13; also elsewhere on the board
CANH: J2.3, J2.11; also elsewhere on the board
CANL: J2.4, J2.12; also elsewhere on the board
CHASSIS_GND: IMD.6, J2.16
CURRENT: CURRENT_SENSE.1, J1.6; also elsewhere on the board
CURRENT_REF: CURRENT_REF.1, J1.7; also elsewhere on the board
CURR_N: CURRENT_SHUNT.3; also elsewhere on the board
CURR_P: CURRENT_SHUNT.2; also elsewhere on the board
EM_CANH: EM.2; also elsewhere on the board
EM_CANL: EM.3; also elsewhere on the board
GND: A1.2 (GND), A2.2 (GND), C1.2, C2.2, C3.2, C4.2, C5.2, C6.2, C17.2, C26.2, C27.2, C28.2, C43.2, CURRENT_SHUNT.4, D2.1 (A), D9.1 (A), D10.1 (A), EM.4, IMD.4, J1.2, J1.4, J1.9, J2.15, Q3.2 (S), Q4.2 (S), R19.1, R46.1, R47.2, R49.1, R73.1, R74.1, R89.1, R94.2, R96.1, R97.1, TP_GND.1, TSB.8, U1.1 (GND), U15.1 (GND), U27.4 (GND), U27.8 (GND); also elsewhere on the board
IMD_OK: J2.7; also elsewhere on the board
ISO_PACK+: TSB.2; also elsewhere on the board
ISO_PACK-: TSB.1; also elsewhere on the board
ISO_TS+: TSB.4; also elsewhere on the board
ISO_TS-: TSB.3; also elsewhere on the board
MHS: IMD.3, R19.2; also elsewhere on the board
unnamed: 3.3V.1 (C), R96.2
unnamed: 5V.1 (C), R73.2
unnamed: C28.1, R68.1, U15.2 (TRIGGER), U15.6 (THRESHOLD)
unnamed: C17.1, U15.5 (CONTROL)
unnamed: R68.2, R69.1, U15.7 (DISCHARGE)
unnamed: 12V.1 (C), R74.2
unnamed: D10.3 (C), R70.1, R94.1, TP_TSAL_GREEN.1, U27.9 (D)
unnamed: D9.3 (C), R47.1, R71.1, TP_TSAL_RED.1, U15.3 (OUTPUT)
unnamed: R95.2, TSAL_GREEN.2 (A)
unnamed: F1.1, J2.10
unnamed: F2.1, J2.9
unnamed: 24V.1 (C), R49.2
unnamed: R72.2, TSAL_RED.2 (A)
unnamed: Q3.1 (G), R71.2
unnamed: Q4.1 (G), R70.2
unnamed: D2.2 (C), D11.2 (C), Q5.2 (S), XF1.1, XF1.2 (1)
unnamed: D11.1 (A), Q5.1 (G), R89.2, R97.2
OKHS: IMD.2; also elsewhere on the board
PRECHARGE_OK: TSB.7; also elsewhere on the board
SHDN: J1.8, J1.10, J2.5, TSB.6
TIMER_EN: R46.2, U15.4 (!RESET), U27.10 (D)
TSAL_GREEN: F2.2, Q4.3 (D), TSAL_GREEN.1 (C)
TSAL_RED: F1.2, Q3.3 (D), TSAL_RED.1 (C)

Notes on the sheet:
Connectors
ACU to TSB connections
Power to ECU, CAN, TSAL, Shutdown Signals
Power Fusing and Regulation
SHDN connnects directly to AIR+, AIR- connects directly to GND
TSAL Circuitry
555 Timer Astable Mode Frequency: 3.529 Hz Duty Cycle: 50.57% Rules say 2-5Hz
SHDN connnects directly to AIR+
Current Sensor Accumulator GND, both AIR+ and -
IMD
Current Shunt
USE Higher watt rated


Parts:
AMS_OK: LED_0603_GREEN; 0603-LED
D3: TVS__8V; SOT-23
IMD_OK: LED_0603_ORANGE; 0603-LED
OKHS: LED_0603_YELLOW; 0603-LED
Q2: TRANSISTOR_N_MOS__PMV15ENEA; SOT-23
R3, R20: RESISTOR_0603_20K; 0603-RES
R4, R21: RESISTOR_0603_5.1K; 0603-RES
R5: RESISTOR_0603_10K; 0603-RES
R6: RESISTOR_0603_10; 0603-RES
R17: RESISTOR_0603_2.2K; 0603-RES
R18, R25, R48: RESISTOR_0603_2K; 0603-RES
TP_AMS_OK: TEST_POINT; MICRO_MINIATURE
TP_IMD_OK: TEST_POINT; MICRO_MINIATURE
U2, U3: RELAY_SOLIDSTATE_NO_DIP-4; DIP-4

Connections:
+24V: R4.2, U2.4 (CONTACT2), U3.4 (CONTACT2); also elsewhere on the board
AMS_OK: AMS_OK.2 (A), R3.2, TP_AMS_OK.1, U2.3 (CONTACT1); also elsewhere on the board
AMS_OK_3.3V: D3.3 (C), R5.1, R6.1; also elsewhere on the board
GND: D3.1 (A), Q2.2 (S), R3.1, R5.2, R17.1, R18.1, R20.1, R25.1, R48.1, U3.2 (CONTROL-); also elsewhere on the board
IMD_OK: IMD_OK.2 (A), R20.2, TP_IMD_OK.1, U3.3 (CONTACT1); also elsewhere on the board
unnamed: R21.2, U3.1 (CONTROL+)
unnamed: OKHS.1 (C), R18.2
unnamed: R4.1, U2.1 (CONTROL+)
unnamed: AMS_OK.1 (C), R48.2
unnamed: Q2.3 (D), U2.2 (CONTROL-)
unnamed: IMD_OK.1 (C), R25.2
unnamed: Q2.1 (G), R6.2
OKHS: OKHS.2 (A), R17.2, R21.1; also elsewhere on the board

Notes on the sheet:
Josh Kirshenbaum
Shutdown Signal Buffering/Amplification


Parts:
C14, C15, C23, C24, C25, C38, C39, C40, C41, C42: CAPACITOR_0603_10V_0.1UF; 0603-CAP
D1: TVS__8V; SOT-23
K1: RELAY_SOLIDSTATE_NO_DIP-4; DIP-4
PACK+_OUT_TEST: TEST_POINT; MICRO_MINIATURE
PC_OK: TEST_POINT; MICRO_MINIATURE
PRECHARGE_OK: LED_0603_RED; 0603-LED
Q1: TRANSISTOR_N_MOS__PMV15ENEA; SOT-23
R1: RESISTOR_0603_10; 0603-RES
R2, R55, R56, R57, R61, R62, R66, R67, R86, R87, R88, R91: RESISTOR_0603_10K; 0603-RES
R24, R65, R83: RESISTOR_0603_1K; 0603-RES
R33, R34, R37, R38: RESISTOR_0603_18.7K_LT; 0603-RES
R35, R36, R39, R40: RESISTOR_0603_43K_LT; 0603-RES
R52, R60, R64, R85: RESISTOR_0603_DNP; 0603-RES
R53: RESISTOR_0603_5.9K; 0603-RES
R54: RESISTOR_0603_11.5K; 0603-RES
R58: RESISTOR_0603_36.5K; 0603-RES
R59: RESISTOR_0603_330K; 0603-RES
R63, R84: RESISTOR_0603_14K; 0603-RES
R90: RESISTOR_0603_73.2K; 0603-RES
R92: RESISTOR_0603_1M; 0603-RES
R93: RESISTOR_0603_8.66K; 0603-RES
R135: RESISTOR_0603_470; 0603-RES
TS+_OUT_TEST: TEST_POINT; MICRO_MINIATURE
U8, U9, U11, U12, U13, U22, U26: OPAMP_1_CHANNEL_OPA991; SC-70-5
U23, U24, U25: LOGICGATE_AND_DCK3; SC-70-5

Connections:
0.90X_DIV: R58.1, R59.2, R60.2, U12.3 (VIN-)
0.525V_DIV: R90.1, R92.2, R93.2, U26.3 (VIN-)
3.305V_DIV: R52.2, R53.1, R54.2, U11.3 (VIN-)
4.66V_DIV_A: R63.2, R64.1, R65.1, U13.1 (VIN+)
4.66V_DIV_B: R83.1, R84.2, R85.1, U22.1 (VIN+)
60V_THRESHOLD: R91.2, U26.4 (VOUT); also elsewhere on the board
+5V: C14.1, C15.1, C23.1, C24.1, C25.1, C38.1, C39.1, C40.1, C41.1, C42.1, K1.4 (CONTACT2), R53.2, R64.2, R65.2, R83.2, R85.2, R90.2, U8.5 (VDD), U9.5 (VDD), U11.5 (VDD), U12.5 (VDD), U13.5 (VDD), U22.5 (VDD), U23.5 (VDD), U24.5 (VDD), U25.5 (VDD), U26.5 (VDD); also elsewhere on the board
AIR2-: Q1.3 (D); also elsewhere on the board
GND: C14.2, C15.2, C23.2, C24.2, C25.2, C38.2, C39.2, C40.2, C41.2, C42.2, D1.1 (A), K1.2 (CONTROL-), PRECHARGE_OK.1 (C), Q1.2 (S), R2.2, R36.2, R39.2, R52.1, R54.1, R56.1, R57.1, R59.1, R60.1, R61.1, R63.1, R66.1, R67.1, R84.1, R86.1, R87.1, R88.1, R91.1, R92.1, R93.1, U8.2 (GND), U9.2 (GND), U11.2 (GND), U12.2 (GND), U13.2 (GND), U22.2 (GND), U23.3 (GND), U24.3 (GND), U25.3 (GND), U26.2 (GND); also elsewhere on the board
HV+_OUT_OK: R87.2, U23.4 (OUT), U25.2 (IN2)
ISO_PACK+: R33.1, R55.2; also elsewhere on the board
ISO_PACK-: R34.1, R55.1; also elsewhere on the board
ISO_TS+: R37.1, R62.2; also elsewhere on the board
ISO_TS-: R38.1, R62.1; also elsewhere on the board
unnamed: PRECHARGE_OK.2 (A), R24.1
unnamed: Q1.1 (G), R1.2
unnamed: R37.2, R39.1, U9.1 (VIN+)
unnamed: R38.2, R40.1, U9.3 (VIN-)
unnamed: R33.2, R36.1, U8.1 (VIN+)
unnamed: R34.2, R35.1, U8.3 (VIN-)
unnamed: K1.1 (CONTROL+), R135.1
unnamed: R135.2, U25.4 (OUT)
PACK+_OUT: PACK+_OUT_TEST.1, R35.2, R57.2, R58.2, U8.4 (VOUT), U11.1 (VIN+), U22.3 (VIN-); also elsewhere on the board
PRECHARGE+_OUT_OK: R88.2, U24.4 (OUT), U25.1 (IN1)
PRECHARGE_OK: D1.3 (C), K1.3 (CONTACT1), PC_OK.1, R1.1, R2.1, R24.2; also elsewhere on the board
PRECHARGE_REACHED: R61.2, U12.4 (VOUT), U24.2 (IN2)
TS+_OUT: R40.2, R66.2, TS+_OUT_TEST.1, U9.4 (VOUT), U12.1 (VIN+), U13.3 (VIN-), U26.1 (VIN+); also elsewhere on the board
TS+_OUT_OV_OK: R67.2, U13.4 (VOUT), U24.1 (IN1)
V_PACK_REF_OV_OK: R86.2, U22.4 (VOUT), U23.1 (IN1)
V_PACK_REF_UV_OK: R56.2, U11.4 (VOUT), U23.2 (IN2)

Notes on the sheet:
60V threshold check
low side switches shutdown current across precharge relay
Josh Kirshenbaum
AIR2- Low Side Switching with PRECHARGE_OK
550V corresponds to 4.816V out of difference op amp
OV fault at 533V
UV fault at 377V
Trips at 59.95V
TSB Outputs: TS: 533V -> 2.02954V TS: 377V -> 1.43553V
OPA991 Gain: 43k/18.7k = 2.2994652
OPA991 Outputs: TS/P: 533V -> 4.66686V TS/P: 377V -> 3.30095V


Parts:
BSPD_CURRENT: TEST_POINT; MICRO_MINIATURE
C8, C16: CAPACITOR_0603_50V_0.1UF; 0603-CAP
C29: CAPACITOR_0603_25V_0.1UF; 0603-CAP
C30, C33, C61: CAPACITOR_0603_10V_0.1UF; 0603-CAP
C31, C36, C62, C65: CAPACITOR_0603_16V_0.47UF; 0603-CAP
C32, C34, C63, C64: CAPACITOR_0603_10V_1UF; 0603-CAP
C55: CAPACITOR_0603_25V_1UF; 0603-CAP
C56, C57: CAPACITOR_0603_10V_68NF; 0603-CAP
CUR_SHUNT: TEST_POINT; 5015
R22, R23: RESISTOR_0603_10.5K; 0603-RES
R41: RESISTOR_0603_DNP; 0603-RES
R42, R44: RESISTOR_0603_2.74K; 0603-RES
R43: RESISTOR_0603_100K; 0603-RES
R75, R77, R106, R107, R108, R109: RESISTOR_0603_10K; 0603-RES
R76, R78, R122, R125, R126, R128, R131, R132: RESISTOR_0603_12K; 0603-RES
R110: RESISTOR_0603_5.1K; 0603-RES
R111: RESISTOR_0603_4.12K; 0603-RES
R123, R124, R129, R130: RESISTOR_0603_7.5K; 0603-RES
R127, R133: RESISTOR_0603_20K; 0603-RES
U4, U5, U16, U18, U33: OPAMP_1_CHANNEL_OPA991; SC-70-5
U17, U19: OPAMP_2_CHANNEL_OPA_2991; SOT-23-8

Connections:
+3V3: C29.1, C30.1, C33.1, C61.1, R108.2, U16.5 (VDD), U17.8 (VDD), U18.5 (VDD), U19.8 (VDD); also elsewhere on the board
+12V: C55.1, U33.5 (VDD); also elsewhere on the board
+24V: C8.1, C16.1, U4.5 (VDD), U5.5 (VDD); also elsewhere on the board
BSPD_CURRENT: BSPD_CURRENT.1, R23.2, U5.4 (VOUT); also elsewhere on the board
BSPD_CURRENT_REF: R22.2, U4.4 (VOUT); also elsewhere on the board
CURRENT: R43.2, U5.1 (VIN+); also elsewhere on the board
CURRENT_REF: R41.2, U4.1 (VIN+); also elsewhere on the board
CURRENT_SHUNT_OUT: C56.1, CUR_SHUNT.1, R110.1, R111.2; also elsewhere on the board
CURR_N: R106.1; also elsewhere on the board
CURR_P: R107.1; also elsewhere on the board
GND: C8.2, C16.2, C29.2, C30.2, C31.2, C33.2, C36.2, C55.2, C56.2, C61.2, C62.2, C65.2, R41.1, R42.1, R43.1, R44.1, R76.2, R78.2, R110.2, R126.1, R127.1, R132.1, R133.1, U4.2 (GND), U5.2 (GND), U16.2 (GND), U17.4 (GND), U18.2 (GND), U19.4 (GND), U33.2 (GND); also elsewhere on the board
unnamed: R23.1, R44.2, U5.3 (VIN-)
unnamed: C34.2, R124.1, R125.2
unnamed: R22.1, R42.2, U4.3 (VIN-)
unnamed: C36.1, R124.2, U17.5 (VIN+)
unnamed: R77.2, R78.1, U18.1 (VIN+)
unnamed: C32.2, R122.2, R123.1
unnamed: C32.1, R125.1, R126.2, U17.1 (VOUT), U17.2 (VIN-)
unnamed: C31.1, R123.2, U17.3 (VIN+)
unnamed: R75.2, R76.1, U16.1 (VIN+)
unnamed: R107.2, R108.1, U33.1 (VIN+)
unnamed: C57.2, R106.2, R109.1, U33.3 (VIN-)
unnamed: C57.1, R109.2, R111.1, U33.4 (VOUT)
unnamed: C64.2, R130.1, R131.2
unnamed: C65.1, R130.2, U19.5 (VIN+)
unnamed: C63.2, R128.2, R129.1
unnamed: C63.1, R131.1, R132.2, U19.1 (VOUT), U19.2 (VIN-)
unnamed: C62.1, R129.2, U19.3 (VIN+)
PACK+_BUFFER: R128.1, U16.3 (VIN-), U16.4 (VOUT)
PACK+_FILTERED: C64.1, R133.2, U19.6 (VIN-), U19.7 (VOUT); also elsewhere on the board
PACK+_OUT: R75.1; also elsewhere on the board
TS+_OUT: R77.1; also elsewhere on the board
TS+_OUT_BUFFER: R122.1, U18.3 (VIN-), U18.4 (VOUT)
TS+_OUT_FILTERED: C34.1, R127.2, U17.6 (VIN-), U17.7 (VOUT); also elsewhere on the board

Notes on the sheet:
Josh Kirshenbaum
Analog Filtering
5V to 24.16V
SSA-250 Current Sensor

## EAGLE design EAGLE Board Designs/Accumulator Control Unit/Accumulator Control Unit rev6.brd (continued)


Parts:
A3: TEENSY_4.0TH; TEENSY_SHORT
C7, C13, C52, C54: CAPACITOR_0603_10V_10NF; 0603-CAP
C9, C18: CAPACITOR_0603_10V_1UF; 0603-CAP
C10, C11, C19, C20, C22, C37, C53: CAPACITOR_0603_10V_0.1UF; 0603-CAP
C12, C21: CAPACITOR_0603_10V_4.7NF; 0603-CAP
D4, D5, D6, D8: TVS_DO-214AA_28V; DO-214AA
D7: TVS__8V; SOT-23
R7, R9, R11: RESISTOR_0603_36.5K; 0603-RES
R8, R10, R12: RESISTOR_0603_4.64K; 0603-RES
R13, R15: RESISTOR_0603_; 0603-RES
R14: RESISTOR_0603_18.7K; 0603-RES
R16: RESISTOR_0603_5.1K; 0603-RES
R26, R27, R50, R51: RESISTOR_0603_60.4; 0603-RES
R28, R29: RESISTOR_0603_2K; 0603-RES
R30, R103: RESISTOR_0603_1.65K; 0603-RES
R31, R80, R82, R104: RESISTOR_0603_470; 0603-RES
R32, R105: RESISTOR_0603_120; 0603-RES
R45, R102: RESISTOR_0603_1K; 0603-RES
R79, R81, R101: RESISTOR_0603_10K; 0603-RES
T1: TRANSFORMER_HM2112ZNLT_AIRGAP; HM2112ZNLT_AIRGAP
TD1, TD2: CONNECTOR-2_MF_T_V_; MOLEX_MICROFIT_PTH_VERTICAL_02_SINGLE
TD+, TD+2: TEST_POINT; MICRO_MINIATURE
TD-, TD-2: TEST_POINT; MICRO_MINIATURE
TEENSY_OK: LED_0603_RED; 0603-LED
U6, U10: TCAN1051HQV-Q1; SOIC-08(NARROW,0.15")
U7, U32: LTC6820; MSOP-16
U20: LOGICGATE_BUFFER; SC-70-5
U21: ADM8316WBX30; SOT-23-5
WATCHDOG: LED_0603_BLUE; 0603-LED
WATCHDOG_INPUT: TEST_POINT; MICRO_MINIATURE

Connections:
3.3V: A3.3.3V
24V_SCALED_3.3V: A3.D19 (A5), R7.2, R8.1
+3V3: C11.2, C13.2, C20.2, C22.1, C37.2, C52.2, C53.1, R28.2, R29.2, R45.2, R102.2, U6.5 (VIO), U7.1 (VDD), U7.6 (VLOGIC), U7.7 (VDD), U7.8 (VDD), U7.9 (VDD), U7.12 (VDD), U10.5 (VIO), U20.5 (VDD), U21.5 (VDD), U32.1 (VDD), U32.6 (VLOGIC), U32.7 (VDD), U32.8 (VDD), U32.9 (VDD), U32.12 (VDD); also elsewhere on the board
+5V: A3.VIN, C9.2, C10.2, C18.2, C19.2, U6.3 (VDD), U10.3 (VDD); also elsewhere on the board
+24V: D4.2 (C), R7.1; also elsewhere on the board
AMS_OK_3.3V: U20.4 (OUT); also elsewhere on the board
BSPD_CURRENT: D5.2 (C), R9.1; also elsewhere on the board
BSPD_CURRENT_TEENSY: A3.D14 (A0), R9.2, R10.1
CANH: R27.2, U6.7 (CANH); also elsewhere on the board
CANL: R26.2, U6.6 (CANL); also elsewhere on the board
CS_LTC_6820: A3.D10 ((CS)D10), R45.1, U7.5 (!CS)
CURRENT_N_FILT: A3.D20 (A6)
CURRENT_P_FILT: A3.D21 (A7)
CURRENT_SHUNT_OUT: A3.D16 (A2); also elsewhere on the board
EM_CANH: R51.2, U10.7 (CANH); also elsewhere on the board
EM_CANL: R50.2, U10.6 (CANL); also elsewhere on the board
EM_CRX: A3.D23 (A9), U10.4 (RXD)
EM_CTX: A3.D22 (A8), U10.1 (TXD)
GND: A3.AGND/GND (GND), A3.GND, C7.2, C9.1, C10.1, C11.1, C12.1, C13.1, C18.1, C19.1, C20.1, C21.1, C22.2, C37.1, C52.1, C53.2, C54.2, D4.1 (A), D5.1 (A), D6.1 (A), D7.1 (A), D8.1 (A), R8.2, R10.2, R12.2, R13.2, R16.2, R31.2, R79.1, R81.1, R101.1, R104.2, TEENSY_OK.1 (C), U6.2 (GND), U6.8 (S), U7.13 (GND), U7.14 (GND), U10.2 (GND), U10.8 (S), U20.3 (GND), U21.2 (GND), U32.13 (GND), U32.14 (GND), WATCHDOG.1 (C); also elsewhere on the board
IM: T1.10 (TD-), U7.10 (IM)
IMD_OK: D6.2 (C), R11.1; also elsewhere on the board
IMD_OK_TEENSY: A3.D3, R11.2, R12.1
IM_2: T1.7 (TD-), U32.10 (IM)
IP: T1.12 (TD+), U7.11 (IP)
IP_2: T1.9 (TD+), U32.11 (IP)
MHS: D8.2 (C), R15.1; also elsewhere on the board
MHS_TEENSY: A3.D7, R15.2, R16.1
unnamed: A3.D11 ((SDO)D11), R29.1, U7.2 (SDI), U32.2 (SDI)
unnamed: R79.2, U20.2 (IN), U21.1 (!RESET!)
unnamed: C12.2, R26.1, R27.1
unnamed: A3.D0 ((CRX1)D0), U6.4 (RXD)
unnamed: A3.D1 ((CTX1)D1), U6.1 (TXD)
unnamed: C21.2, R50.1, R51.1
unnamed: R30.1, U7.16 (IBIAS)
unnamed: R30.2, R31.1, U7.15 (ICMP)
unnamed: R103.1, U32.16 (IBIAS)
unnamed: C7.1, T1.11 (TCT)
unnamed: A3.D9, R102.1, U32.5 (!CS)
unnamed: R103.2, R104.1, U32.15 (ICMP)
unnamed: A3.D12 ((SDI)D12), R28.1, U7.3 (SDO), U32.3 (SDO)
unnamed: A3.D13 ((CLK)D13), U7.4 (CLK), U32.4 (CLK)
unnamed: R80.1, WATCHDOG.2 (A)
unnamed: R82.1, TEENSY_OK.2 (A)
unnamed: C54.1, T1.8 (TCT)
PACK+_FILTERED: A3.D17 (A3); also elsewhere on the board
PRECHARGE_OK: D7.3 (C), R14.1; also elsewhere on the board
PRECHARGE_OK_TEENSY: A3.D4, R13.1, R14.2
TD1+: R32.2, T1.4 (MX+), TD1.1, TD+.1
TD1-: R32.1, T1.6 (MX-), TD1.2, TD-.1
TD2+: R105.2, T1.1 (MX+), TD2.1, TD+2.1
TD2-: R105.1, T1.3 (MX-), TD2.2, TD-2.1
TEENSY_OK: A3.D6, R82.2, R101.2, U21.3 (!MR!)
TS+_OUT_FILTERED: A3.D18 (A4); also elsewhere on the board
WATCHDOG_INPUT: A3.D5, R80.2, R81.2, U21.4 (WDI), WATCHDOG_INPUT.1

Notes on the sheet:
24V to 3.3V
5V to 3.3V
Watchdog Timer
Voltage Dividers
LTC6820 and Transformer
22V to 3.3V



Board: 4 copper layers, 255.0 x 73.0 mm, 286 parts (4 on the bottom side), 136 nets.

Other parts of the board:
U$1, U$2, U$3, U$4, U$5, U$6: MOUNTING_M4
U$7, U$8: MOUNTING_M3
U$9: TS
U$10, U$11, U$13, U$14, U$15, U$101: HV_MEDIUM
U$12: LOGO_HYTECH_SQUARE_EXTRA_LARGE
U$16: LOGO_HYTECH_LARGE
U$17: LOGO_GT_MEDIUM
U$19: DANGER_HIGH_VOLTAGE

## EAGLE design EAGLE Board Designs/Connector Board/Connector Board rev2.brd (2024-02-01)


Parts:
ACCEL1, ACCEL2: JUMPER__1X02; 1X02
BRAKE1, BRAKE2: JUMPER__1X02; 1X02
CANH_2, CANH_3: TEST_POINT; 5015
CANL_2, CANL_3: TEST_POINT; 5015
J1: CONNECTOR-20_MF_T_V_; MOLEX_MICROFIT_PTH_VERTICAL_20_DUAL
J2, J3, J12, J14: CONNECTOR-8_μF_T_V_BLACK; MOLEX_MICROFIT_PTH_VERTICAL_08_DUAL
J4, J13: CONNECTOR-2_MF_T_V_; MOLEX_MICROFIT_PTH_VERTICAL_02_SINGLE
J5, J8, J9: CONNECTOR-4_μF_T_V_BLACK; MOLEX_MICROFIT_PTH_VERTICAL_04_DUAL
J6, J7: CONNECTOR-24_CONNECTOR-24_; EHT-112-01
J15: CONNECTOR-10_MF_T_V_; MOLEX_MICROFIT_PTH_VERTICAL_10_DUAL

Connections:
+5V: J2.2, J3.2, J6.24, J14.1, J15.1, J15.2, J15.3
+24V: J1.10, J1.20, J6.22, J12.1; also elsewhere on the board
ACCEL_1_EXT: ACCEL1.2, J15.4
ACCEL_2_EXT: ACCEL2.2, J15.5
BMS_OK: J1.14, J7.7
BRAKELIGHT_12V: J1.17; also elsewhere on the board
BRAKELIGHT_EN: J7.10; also elsewhere on the board
BRAKE_1_EXT: BRAKE1.2, J15.7
BRAKE_2_EXT: BRAKE2.2, J15.6
CANH_2: CANH_2.1, J1.1, J1.4, J6.19
CANH_3: CANH_3.1, J1.6, J6.16, J12.3
CANL_2: CANL_2.1, J1.2, J1.3, J6.20
CANL_3: CANL_3.1, J1.5, J6.17, J12.4
CB_VIN: J2.1, J3.1; also elsewhere on the board
CURRENT_EXT: J1.12, J7.11
FL_CORNER_EXT_N: J2.4, J6.2
FL_CORNER_EXT_P: J2.3, J6.1
FR_CORNER_EXT_N: J3.4, J6.5
FR_CORNER_EXT_P: J3.3, J6.6
GND: J1.9, J1.19, J2.7, J3.7, J4.1, J6.3, J6.4, J6.7, J6.8, J6.11, J6.12, J6.15, J6.18, J6.21, J6.23, J12.8, J13.1, J14.8, J15.8, J15.9, J15.10; also elsewhere on the board
INVERTER_24V_EN: J7.8; also elsewhere on the board
INVERTER_24V_EN_BOOSTED: J1.15; also elsewhere on the board
INVERTER_EN: J7.6; also elsewhere on the board
INVERTER_EN_BOOSTED: J1.16; also elsewhere on the board
LATCH_BTN: J1.18, J7.13, J7.14
unnamed: ACCEL1.1, J7.15
unnamed: ACCEL2.1, J7.16
unnamed: BRAKE2.1, J7.17
unnamed: BRAKE1.1, J7.18
OKHS_IN: J1.13, J7.9
REFERENCE_EXT: J1.11, J7.12
SHDN_A: J5.1, J5.2; also elsewhere on the board
SHDN_B: J5.3, J5.4, J7.23, J7.24, J12.5
SHDN_G: J2.5, J7.1, J7.2
SHDN_H: J2.6, J3.8
SHDN_I: J3.6, J8.1, J8.2
SHDN_J: J7.5, J8.3, J8.4, J9.1, J9.2, J12.2
SHDN_K: J1.7, J1.8, J9.3, J9.4, J12.6
STEERING_1_EXT: J7.19, J14.7
STEERING_2_EXT: J7.20, J14.6
STEERING_RX_N: J6.14, J14.5
STEERING_RX_P: J6.13, J14.2
STEERING_TX_N: J6.10, J14.4
STEERING_TX_P: J6.9, J14.3
THERM_FL_EXT: J7.3, J13.2
THERM_FR_EXT: J4.2, J7.4

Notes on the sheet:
BOTS
Inertia
BRB
ADD stitching vias
Accel/brake pedals
Dashboard
Steering RS422
FL corner board
FR corner board
Firewall
Main ECU Board dimension line up exactly
Thermistors


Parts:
A1: VOLTAGE_REGULATOR_MODULE_OKI-78SR_12V; OKI-78SR
D1, D2, D3, D4, D5, D6: TVS__15V; SOT-23
JP1, JP2: JUMPER_0603_; 0603-RES
Q1, Q3, Q5: TRANSISTOR_N_MOS__DMG3406L-7; SOT-23
Q2, Q4, Q6: TRANSISTOR_P_MOS_SOT-23_DMP3056L-7; SOT-23
R5, R8, R11, R12: RESISTOR_0603_10K; 0603-RES
R6, R7, R9, R10: RESISTOR_0603_5.1K; 0603-RES
XF1: FUSE_HOLDER_MINIBLADESMD; 3588

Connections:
+12V: A1.3 (OUT), D5.3 (C), JP2.1, Q6.2 (S), R11.2
+24V: A1.1 (IN), D2.3 (C), D4.3 (C), JP1.1, Q2.2 (S), Q4.2 (S), R7.2, R10.2, XF1.1, XF1.2 (1); also elsewhere on the board
BRAKELIGHT_12V: Q6.3 (D); also elsewhere on the board
BRAKELIGHT_EN: D6.3 (C), Q5.1 (G), R12.2; also elsewhere on the board
CB_VIN: JP1.2, JP2.2; also elsewhere on the board
GND: A1.2 (GND), D1.1 (A), D3.1 (A), D6.1 (A), Q1.2 (S), Q3.2 (S), Q5.2 (S), R5.1, R8.1, R12.1; also elsewhere on the board
INVERTER_24V_EN: D1.3 (C), Q1.1 (G), R5.2; also elsewhere on the board
INVERTER_24V_EN_BOOSTED: Q2.3 (D); also elsewhere on the board
INVERTER_EN: D3.3 (C), Q3.1 (G), R8.2; also elsewhere on the board
INVERTER_EN_BOOSTED: Q4.3 (D); also elsewhere on the board
unnamed: D2.1 (A), Q2.1 (G), R6.2, R7.1
unnamed: Q1.3 (D), R6.1
unnamed: D4.1 (A), Q4.1 (G), R9.2, R10.1
unnamed: Q3.3 (D), R9.1
unnamed: D5.1 (A), Q5.3 (D), Q6.1 (G), R11.1
SHDN_A: XF1.3 (2), XF1.4 (2); also elsewhere on the board

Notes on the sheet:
power consumption could potentially be too high at 24V for the voltage reference on the corner board


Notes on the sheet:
2-pin
4-pin
8-pin
10-pin
20-pin



Board: 4 copper layers, 97.5 x 50.8 mm, 51 parts (22 on the bottom side), 52 nets.

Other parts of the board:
U$4, U$5, U$6, U$7: MOUNTING_M3
U$11: LOGO_GT_MEDIUM
U$14: LOGO_HYTECH_SMALL

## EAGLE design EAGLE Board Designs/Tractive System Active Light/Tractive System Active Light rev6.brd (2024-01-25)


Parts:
D1, D2, D3, D4: LED_RGB_ASMG-PT00-00001; ASMG-PT00-00001
J1: CONNECTOR-4_μF_S_RA_; MOLEX_MICROFIT_SMD_RIGHTANGLE_04_DUAL
R1: RESISTOR_0805_36; 0805-RES
R3: RESISTOR_0805_5.1; 0805-RES

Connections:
+12V: J1.1, R1.1, R3.1
GND_GREEN: D4.2 (GREEN-), J1.4
GND_RED: D4.1 (RED-), J1.3
unnamed: D3.1 (RED-), D4.4 (RED+), D4.THERMAL (RED+)
unnamed: D3.2 (GREEN-), D4.5 (GREEN+)
unnamed: D2.1 (RED-), D3.4 (RED+), D3.THERMAL (RED+)
unnamed: D2.2 (GREEN-), D3.5 (GREEN+)
unnamed: D1.1 (RED-), D2.4 (RED+), D2.THERMAL (RED+)
unnamed: D1.2 (GREEN-), D2.5 (GREEN+)
unnamed: D1.4 (RED+), D1.THERMAL (RED+), R1.2
unnamed: D1.5 (GREEN+), R3.2


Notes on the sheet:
External components for ordering



Board: 2 copper layers, 52.2 x 41.5 mm, 10 parts (4 on the bottom side), 11 nets.

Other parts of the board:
U$1, U$3: MOUNTING_M3
U$2: LOGO_HYTECH_MEDIUM

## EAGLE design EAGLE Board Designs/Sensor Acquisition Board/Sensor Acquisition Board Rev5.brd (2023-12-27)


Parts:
CAN_H: TEST_POINT; 5015
CAN_L: TEST_POINT; 5015
J1, J6, J14, J16: CONNECTOR-8_μF_T_V_BLACK; MOLEX_MICROFIT_PTH_VERTICAL_08_DUAL
J2, J3, J7, J13, J15: CONNECTOR-4_μF_T_V_BLACK; MOLEX_MICROFIT_PTH_VERTICAL_04_DUAL
J4, J5, J9: CONNECTOR-4_μF_S_RA_; MOLEX_MICROFIT_SMD_RIGHTANGLE_04_DUAL
J8: CONNECTOR-2_μF_T_V_BLACK; MOLEX_MICROFIT_PTH_VERTICAL_02_DUAL
J10: CONNECTOR-10_MF_T_V_; MOLEX_MICROFIT_PTH_VERTICAL_10_DUAL
J11: CONNECTOR-2_MICROFIT_SMD_RIGHTANGLE_02_SINGLE_BLA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; MOLEX_MICROFIT_SMD_RIGHTANGLE_02_SINGLE
J12: CONNECTOR-6_μF_T_V_BLACK; MOLEX_MICROFIT_PTH_VERTICAL_06_DUAL
JP5V, JP12V, JP24V: JUMPER_0603_; 0603-RES
RH_N: TEST_POINT; 5015
RH_P: TEST_POINT; 5015
RXD: TEST_POINT; 5015
TXD: TEST_POINT; 5015

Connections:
24VIN: J11.1; also elsewhere on the board
+5V: J14.3, J16.3, JP5V.2; also elsewhere on the board
+12V: J2.1, J3.1, J4.1, J5.1, J7.1, J9.1, J10.1, JP12V.2; also elsewhere on the board
+24V: J12.1, J14.4, J15.1, J16.4, JP24V.2; also elsewhere on the board
CAN_N: CAN_L.1, J4.3, J5.3, J9.3, J12.3, J13.3, J15.3; also elsewhere on the board
CAN_P: CAN_H.1, J4.4, J5.4, J9.4, J12.2, J13.2, J15.2; also elsewhere on the board
GND: J1.1, J1.2, J1.3, J1.4, J2.2, J3.2, J4.2, J5.2, J6.1, J6.2, J6.3, J6.4, J7.2, J8.2, J9.2, J10.5, J11.2, J12.6, J13.4, J14.1, J15.4, J16.1; also elsewhere on the board
GPS_PPS: J10.10; also elsewhere on the board
unnamed: J13.1, JP5V.1, JP12V.1, JP24V.1
PI_SHUTDOWN: J8.1; also elsewhere on the board
RESTORE: J10.6; also elsewhere on the board
RHEIGHT_N: J2.3, J3.3, J7.3, RH_N.1; also elsewhere on the board
RHEIGHT_P: J2.4, J3.4, J7.4, RH_P.1; also elsewhere on the board
RL_EXT_N: J14.6; also elsewhere on the board
RL_EXT_P: J14.5; also elsewhere on the board
RR_EXT_N: J16.6; also elsewhere on the board
RR_EXT_P: J16.5; also elsewhere on the board
RXD_232: J10.2, RXD.1; also elsewhere on the board
SHDN_K: J12.4, J14.7
SHDN_L: J14.8, J16.7
SHDN_M: J12.5, J16.2
SYNC_IN: J10.7; also elsewhere on the board
SYNC_OUT: J10.4; also elsewhere on the board
THERM1: J6.8; also elsewhere on the board
THERM2: J6.7; also elsewhere on the board
THERM3: J6.6; also elsewhere on the board
THERM4: J6.5; also elsewhere on the board
THERM5: J1.8; also elsewhere on the board
THERM6: J1.7; also elsewhere on the board
THERM7: J1.6; also elsewhere on the board
THERM8: J1.5; also elsewhere on the board
TXD_232: J10.3, TXD.1; also elsewhere on the board

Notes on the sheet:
Thermistor x8 2 pin each Varied resistance Vertical
Ride height sensor x4 RS485 multidrop Vertical
RL & RR
Aero sensors CAN Vertical
8-channel
64-channel
IMU 10 pin molex 1. RS232 data 2. Power supply Vertical
GLV Power and gnd Vertical
Corner board 1. ADC isoSPI master 2. Power supply 3. Interlock Vertical
CAN 1. Main ECU -> SAB 2. SAB -> TCU/pi 3. Spare Vertical
Distinguish connectors: Color markers Tapes CAN & RS485 Thermistor & corner board
Main ECU Do not connect 24V
Test rail being used Could reduce in next rev
24VIN instead Consider for future rev
Fault prevention: Plug in connector from wrong side SHDN discontinuous GND and supply rails still match
Cecilia Yang
Liwei Sun
Pi shutdown button Vertical
TCU
Spare CAN Various power choices


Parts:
3V3, 5V, 12V: TEST_POINT; 5015
A1: VOLTAGE_REGULATOR_MODULE_OKI-78SR_12V; OKI-78SR
A2: VOLTAGE_REGULATOR_MODULE_OKI-78SR_5V; OKI-78SR
C1, C2, C4: CAPACITOR_0805_50V_10UF; 0805-CAP
C3, C5, C6: CAPACITOR_0603_25V_10UF; 0603-CAP
C7: CAPACITOR_ELECTROLYTIC_EEH_AZS_470UF; EEH-AZS
D1: LED_0603_RED; 0603-LED
D2: LED_0603_YELLOW; 0603-LED
D3: LED_0603_GREEN; 0603-LED
D4: TVS_DO-219AB_14V; SMF
D6: TVS_DO-214AA_30V; 1.5SMBJ
GND: TEST_POINT; 5015
R1: RESISTOR_0603_1K; 0603-RES
R2: RESISTOR_0603_240; 0603-RES
R3: RESISTOR_0603_120; 0603-RES
U1: VOLTAGE_REGULATOR_SOT-223_3.3V; SOT-223
XF1: FUSE_HOLDER_MINIBLADESMD; 3588

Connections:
24VIN: D6.2 (C), XF1.1, XF1.2 (1); also elsewhere on the board
+3V3: 3V3.1, C6.1, R3.1, U1.2 (OUT), U1.4 (OUT); also elsewhere on the board
+5V: 5V.1, A2.3 (OUT), C3.1, C5.1, R2.1, U1.3 (IN); also elsewhere on the board
+12V: 12V.1, A1.3 (OUT), C4.1, D4.P$2 (C), R1.1; also elsewhere on the board
+24V: A1.1 (IN), A2.1 (IN), C1.1, C2.1, C7.PLUS, XF1.3 (2), XF1.4 (2); also elsewhere on the board
GND: A1.2 (GND), A2.2 (GND), C1.2, C2.2, C3.2, C4.2, C5.2, C6.2, C7.MINUS, D1.1 (C), D2.1 (C), D3.1 (C), D4.P$1 (A), D6.1 (A), GND.1, U1.1 (GND); also elsewhere on the board
unnamed: D1.2 (A), R1.2
unnamed: D2.2 (A), R2.2
unnamed: D3.2 (A), R3.2

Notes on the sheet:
Voltage regulators
24V -> 12V Aero sensor Ride height Thermistor IMU
Fuse GLV 24V
Power indication LEDs
Overvoltage protection IMU
Cannot add 5V TVS Always clamping if same voltage as supply
Bulk cap Might not need this large capacity
Cecilia Yang
Possible RPPs: Shottky with higher current MOSFET


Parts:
C8, C9, C10, C11, C12, C13, C14, C15: CAPACITOR_0603_10V_1UF; 0603-CAP
R4, R5, R6, R7, R8, R9, R10, R11: RESISTOR_0603_8.35K; 0603-RES

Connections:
+3V3: R4.1, R5.1, R6.1, R7.1, R8.1, R9.1, R10.1, R11.1; also elsewhere on the board
GND: C8.2, C9.2, C10.2, C11.2, C12.2, C13.2, C14.2, C15.2; also elsewhere on the board
THERM1: C8.1, R4.2; also elsewhere on the board
THERM2: C9.1, R5.2; also elsewhere on the board
THERM3: C10.1, R6.2; also elsewhere on the board
THERM4: C11.1, R7.2; also elsewhere on the board
THERM5: C12.1, R8.2; also elsewhere on the board
THERM6: C13.1, R9.2; also elsewhere on the board
THERM7: C14.1, R10.2; also elsewhere on the board
THERM8: C15.1, R11.2; also elsewhere on the board

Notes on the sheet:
Thermistors
Filter analog input
Resistor select: Geometric mean Largest change in voltage range given target temperature range
Future consideration: adjustable lin reg more current output
Cecilia Yang
Got rid of max's Switched to passives
1uF 0603 caps: 3dB fc @ 35Hz fc = (R1+R2)/(2*pi*R1*R2*C) R1: resistor in series R2: thermistor nominal


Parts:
C48, C49, C50, C51, C52: CAPACITOR_0603_35V_0.1UF; 0603-CAP
C53: CAPACITOR_0603_35V_1UF; 0603-CAP
C54, C55: CAPACITOR_0603_10V_0.1UF; 0603-CAP
C56, C57: CAPACITOR_0603_10V_1UF; 0603-CAP
C58, C59: CAPACITOR_0603_10V_15PF; 0603-CAP
D7: TVS_BIDIRECTIONAL_DUAL; SC-70-3
R12, R13: RESISTOR_0603_2K; 0603-RES
R14, R16: RESISTOR_0603_1.33K; 0603-RES
R15, R17: RESISTOR_0603_1.13K; 0603-RES
R18, R19: RESISTOR_0603_120; 0603-RES
RL_IM: TEST_POINT; 5015
RL_IP: TEST_POINT; 5015
RR_IM: TEST_POINT; 5015
RR_IP: TEST_POINT; 5015
T1, T2: 78613/3C_78613/3C; 78613/3C
U10: MAX3227; SSOP-16
U11, U12: LTC6820; MSOP-16

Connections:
!ADC1_CS: U11.5 (!CS); also elsewhere on the board
!ADC2_CS: U12.5 (!CS); also elsewhere on the board
+3V3: C52.1, C53.1, C54.1, C55.1, C56.1, C57.1, R12.2, R13.2, U10.12 (FORCEON), U10.15 (VCC), U10.16 (!FORCEOFF), U11.1 (EN), U11.6 (VLOGIC), U11.9 (VDD), U11.12 (MSTR), U12.1 (EN), U12.6 (VLOGIC), U12.9 (VDD), U12.12 (MSTR); also elsewhere on the board
GND: C50.1, C51.1, C52.2, C53.2, C54.2, C55.2, C56.2, C57.2, C58.2, C59.2, D7.3 (A), R15.1, R17.1, U10.14 (GND), U11.7 (POL), U11.8 (PHA), U11.13 (SLOW), U11.14 (GND), U12.7 (POL), U12.8 (PHA), U12.13 (SLOW), U12.14 (GND); also elsewhere on the board
unnamed: C50.2, U10.3 (V+)
unnamed: C48.1, U10.2 (C1+)
unnamed: C51.2, U10.7 (V-)
unnamed: R16.2, U12.16 (IBIAS)
unnamed: R16.1, R17.2, U12.15 (ICMP)
unnamed: R14.2, U11.16 (IBIAS)
unnamed: R14.1, R15.2, U11.15 (ICMP)
unnamed: C58.1, T1.2 (PRI_CENTER_TAP)
unnamed: C59.1, T2.2 (PRI_CENTER_TAP)
unnamed: C48.2, U10.4 (C1-)
unnamed: C49.1, U10.5 (C2+)
unnamed: C49.2, U10.6 (C2-)
RL_EXT_N: T1.4 (SEC_1); also elsewhere on the board
RL_EXT_P: T1.6 (SEC_2); also elsewhere on the board
RL_N: R18.1, RL_IM.1, T1.3 (PRI_2), U11.10 (IM)
RL_P: R18.2, RL_IP.1, T1.1 (PRI_1), U11.11 (IP)
RR_EXT_N: T2.4 (SEC_1); also elsewhere on the board
RR_EXT_P: T2.6 (SEC_2); also elsewhere on the board
RR_N: R19.1, RR_IM.1, T2.3 (PRI_2), U12.10 (IM)
RR_P: R19.2, RR_IP.1, T2.1 (PRI_1), U12.11 (IP)
RXD_232: D7.2 (C2), U10.8 (R1IN); also elsewhere on the board
RX_232: U10.9 (R1OUT); also elsewhere on the board
TEENSY_CLK: U11.4 (CLK), U12.4 (CLK); also elsewhere on the board
TEENSY_SDI: R12.1, R13.1, U11.3 (SDO), U12.3 (SDO); also elsewhere on the board
TEENSY_SDO: U11.2 (SDI), U12.2 (SDI); also elsewhere on the board
TXD_232: D7.1 (C1), U10.13 (T1OUT); also elsewhere on the board
TX_232: U10.11 (T1IN); also elsewhere on the board

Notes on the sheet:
isoSPI Rear corner board ADCs
DNP possible Teensy seems to have internal pull-ups
Data output needs pull up Teensy master -> SDO on LTC
IMU RS232 transceiver/level shifter
ESD protection
Cecilia Yang
differential I2C


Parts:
A3: TEENSY_4.0SM; TEENSY_SHORT_SSM
C60: CAPACITOR_0603_10V_4.7NF; 0603-CAP
C61: CAPACITOR_0603_10V_4.7UF; 0603-CAP
C62: CAPACITOR_0603_35V_0.1UF; 0603-CAP
C63, C65, C66, C67: CAPACITOR_0603_10V_0.1UF; 0603-CAP
C64: CAPACITOR_0603_35V_1UF; 0603-CAP
C68, C69: CAPACITOR_0603_10V_1UF; 0603-CAP
CLK: TEST_POINT; 5015
D8, D10: TVS_BIDIRECTIONAL_DUALRS422; SOT-23
D9, D11, D12: TVS_BIDIRECTIONAL_DUAL; SC-70-3
JP4, JP5, JP6: JUMPER_0603_; 0603-RES
MISO: TEST_POINT; 5015
MOSI: TEST_POINT; 5015
R20: RESISTOR_0603_120; 0603-RES
R21, R22: RESISTOR_0603_60.4; 0603-RES
U13: TCAN1051HQV-Q1; SOIC-08(NARROW,0.15")
U14: MAX3075; SOIC-08(NARROW,0.15")
U15: MCP3208; SOIC-16

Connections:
3.3V: A3.3.3V
!ADC1_CS: A3.D2; also elsewhere on the board
!ADC2_CS: A3.D3; also elsewhere on the board
!ADC3_CS: A3.D10 ((CS)D10), U15.10 (!CS!/SHDN)
+3V3: C62.1, C64.1, C65.1, C66.1, C68.1, U13.5 (VIO), U14.8 (VCC), U15.15 (VREF), U15.16 (VDD); also elsewhere on the board
+5V: A3.VIN, C61.1, C63.1, C67.1, C69.1, U13.3 (VDD); also elsewhere on the board
CAN_N: D9.2 (C2), D11.2 (C2), D12.2 (C2), JP4.1, U13.6 (CANL); also elsewhere on the board
CAN_P: D9.1 (C1), D11.1 (C1), D12.1 (C1), JP6.2, U13.7 (CANH); also elsewhere on the board
EN_485: A3.D18 (A4), U14.2 (!RE), U14.3 (DE)
GND: A3.AGND/GND (GND), A3.GND, C60.2, C61.2, C62.2, C63.2, C64.2, C65.2, C66.2, C67.2, C68.2, C69.2, D8.3 (A), D9.3 (A), D10.3 (A), D11.3 (A), D12.3 (A), U13.2 (GND), U13.8 (S), U14.5 (GND), U15.9 (GND), U15.14 (AGND); also elsewhere on the board
GPS_PPS: A3.D4; also elsewhere on the board
unnamed: JP5.1, R20.2
unnamed: JP4.2, R21.1
unnamed: C60.1, R21.2, R22.1
unnamed: JP6.1, R22.2
PI_SHUTDOWN: A3.D14 (A0); also elsewhere on the board
RESTORE: A3.D9; also elsewhere on the board
RHEIGHT_N: D8.2 (C2), D10.2 (C2), JP5.2, U14.7 (B); also elsewhere on the board
RHEIGHT_P: D8.1 (C1), D10.1 (C1), R20.1, U14.6 (A); also elsewhere on the board
RX_232: A3.D7; also elsewhere on the board
RX_485: A3.D16 (A2), U14.1 (RO)
SYNC_IN: A3.D6; also elsewhere on the board
SYNC_OUT: A3.D5; also elsewhere on the board
TEENSY_CAN_RX1: A3.D0 ((CRX1)D0), U13.4 (RXD)
TEENSY_CAN_TX1: A3.D1 ((CTX1)D1), U13.1 (TXD)
TEENSY_CLK: A3.D13 ((CLK)D13), CLK.1, U15.13 (CLK); also elsewhere on the board
TEENSY_SDI: A3.D12 ((SDI)D12), MISO.1, U15.12 (SDO); also elsewhere on the board
TEENSY_SDO: A3.D11 ((SDO)D11), MOSI.1, U15.11 (SDI); also elsewhere on the board
THERM1: U15.1 (CH0); also elsewhere on the board
THERM2: U15.2 (CH1); also elsewhere on the board
THERM3: U15.3 (CH2); also elsewhere on the board
THERM4: U15.4 (CH3); also elsewhere on the board
THERM5: U15.5 (CH4); also elsewhere on the board
THERM6: U15.6 (CH5); also elsewhere on the board
THERM7: U15.7 (CH6); also elsewhere on the board
THERM8: U15.8 (CH7); also elsewhere on the board
TX_232: A3.D8; also elsewhere on the board
TX_485: A3.D17 (A3), U14.4 (DI)

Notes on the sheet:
CAN transceiver and termination Bidirectional TVS/ESD protection
RS485 transceiver Bidirectional TVS/ESD protection Ride height sensors
s tie to gnd
Jumper x 2 Only unjump one side would low pass filter CAN
DNP termination resistors Stub line length in theory is short enough
ADC Digitize analog signals Thermistors
Cecilia Yang



Board: 4 copper layers, 199.5 x 74.3 mm, 130 parts (10 on the bottom side), 69 nets.

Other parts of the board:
U$1: LOGO_HYTECH_MEDIUM
U$2: LOGO_GT_MEDIUM
U$3, U$4, U$5, U$6: MOUNTING_M3
U$7, U$8: LOGO_HYTECH_SQUARE_LARGE

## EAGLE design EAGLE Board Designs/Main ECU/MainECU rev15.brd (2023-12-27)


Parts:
C21, C23: CAPACITOR_0603_10V_15PF; 0603-CAP
D2: SCHOTTKY_1206_40V; 1206-DIODE
J1, J2: CONNECTOR-24_CONNECTOR-24_; EHT-112-01
R55, R56: RESISTOR_0603_120; 0603-RES
T1: TRANSFORMER_HM2112ZNLT; HM2112ZNLT

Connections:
+5V: J1.24; also elsewhere on the board
+24V: D2.2 (C); also elsewhere on the board
ACCEL_1_EXT: J2.15; also elsewhere on the board
ACCEL_2_EXT: J2.16; also elsewhere on the board
BMS_OK: J2.7; also elsewhere on the board
BRAKELIGHT_EN: J2.10; also elsewhere on the board
BRAKE_1_EXT: J2.18; also elsewhere on the board
BRAKE_2_EXT: J2.17; also elsewhere on the board
CANH_2: J1.20; also elsewhere on the board
CANH_3: J1.16; also elsewhere on the board
CANL_2: J1.19; also elsewhere on the board
CANL_3: J1.17; also elsewhere on the board
CURRENT_EXT: J2.11; also elsewhere on the board
FL_CORNER_EXT_N: J1.2, T1.6 (MX-)
FL_CORNER_EXT_P: J1.1, T1.4 (MX+)
FL_CORNER_N: R55.1, T1.7 (TD-); also elsewhere on the board
FL_CORNER_P: R55.2, T1.9 (TD+); also elsewhere on the board
FR_CORNER_EXT_N: J1.5, T1.3 (MX-)
FR_CORNER_EXT_P: J1.6, T1.1 (MX+)
FR_CORNER_N: R56.1, T1.10 (TD-); also elsewhere on the board
FR_CORNER_P: R56.2, T1.12 (TD+); also elsewhere on the board
GND: C21.2, C23.2, J1.3, J1.4, J1.7, J1.8, J1.11, J1.12, J1.15, J1.18, J1.21, J1.23; also elsewhere on the board
INERTIA_SENSE_EXT: J2.5; also elsewhere on the board
INVERTER_24V_EN: J2.8; also elsewhere on the board
INVERTER_EN: J2.6; also elsewhere on the board
LATCH_BTN: J2.13, J2.14; also elsewhere on the board
unnamed: C21.1, T1.11 (TCT)
unnamed: C23.1, T1.8 (TCT)
unnamed: D2.1 (A), J1.22
OKHS_IN: J2.9; also elsewhere on the board
REFERENCE_EXT: J2.12; also elsewhere on the board
RS422_RX_N: J1.14; also elsewhere on the board
RS422_RX_P: J1.13; also elsewhere on the board
RS422_TX_N: J1.10; also elsewhere on the board
RS422_TX_P: J1.9; also elsewhere on the board
SHDN_B: J2.23, J2.24; also elsewhere on the board
SHDN_G: J2.1, J2.2; also elsewhere on the board
STEERING_1_EXT: J2.19; also elsewhere on the board
STEERING_2_EXT: J2.21; also elsewhere on the board
THERM_FL: J2.3; also elsewhere on the board
THERM_FR: J2.4; also elsewhere on the board

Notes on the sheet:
EXTERNAL CONNECTORS
IsoSPI


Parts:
3V3, 5V0: LED_0603_YELLOW; 0603-LED
A1: VOLTAGE_REGULATOR_MODULE_OKI-78SR_5V; OKI-78SR(VERTICAL)
B: LED_0603_GREEN; 0603-LED
BMS: LED_0603_ORANGE; 0603-LED
BSPD: LED_0603_GREEN; 0603-LED
B_HI: LED_0603_RED; 0603-LED
B_MIS: LED_0603_RED; 0603-LED
C: LED_0603_GREEN; 0603-LED
C3: CAPACITOR_ELECTROLYTIC_EEH_AZS_470UF; EEH-AZS
C4, C5, C28: CAPACITOR_0603_25V_10UF; 0603-CAP
C24, C61: CAPACITOR_0603_10V_4.7NF; 0603-CAP
C27: CAPACITOR_0805_50V_10UF; 0805-CAP
C_HI: LED_0603_RED; 0603-LED
C_MIS: LED_0603_RED; 0603-LED
D: LED_0603_GREEN; 0603-LED
D23, D24: TVS_BIDIRECTIONAL_DUAL; SC-70-3
E: LED_0603_GREEN; 0603-LED
F: LED_0603_GREEN; 0603-LED
G: LED_0603_GREEN; 0603-LED
IMD: LED_0603_ORANGE; 0603-LED
JP1, JP3: JUMPER__1X02; 1X02
JP2, JP10: JUMPER_0603_; 0603-RES
LATCH: LED_0603_WHITE; 0603-LED
R5, R8, R11, R14, R17, R20, R24, R25, R26, R27: RESISTOR_0603_2K; 0603-RES
R23, R30: RESISTOR_0603_120; 0603-RES
R28: RESISTOR_0603_180; 0603-RES
R29, R41, R44, R48, R49: RESISTOR_0603_240; 0603-RES
R47, R52, R141, R142: RESISTOR_0603_60.4; 0603-RES
SWOK: LED_0603_ORANGE; 0603-LED
TP1, TP2: TEST_POINT; 5015
U1: VOLTAGE_REGULATOR_SOT-223_3.3V; SOT-223
WDOG: LED_0603_ORANGE; 0603-LED

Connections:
+3V3: C5.1, R30.1, TP2.1, U1.2 (OUT), U1.4 (OUT); also elsewhere on the board
+5V: A1.3 (OUT), C4.1, C28.1, R28.2, R29.1, TP1.1, U1.3 (IN); also elsewhere on the board
+24V: A1.1 (IN), C3.PLUS, C27.1; also elsewhere on the board
BMS_OK: R26.1; also elsewhere on the board
BRAKE_HIGH: R41.1; also elsewhere on the board
BRAKE_MISSING: R49.1; also elsewhere on the board
BSPD_OK: R25.1; also elsewhere on the board
CANH_2: D23.2 (C2), JP10.2; also elsewhere on the board
CANH_3: D24.2 (C2), JP1.2; also elsewhere on the board
CANL_2: D23.1 (C1), JP2.1; also elsewhere on the board
CANL_3: D24.1 (C1), JP3.1; also elsewhere on the board
CURRENT_HIGH: R44.1; also elsewhere on the board
CURRENT_MISSING: R48.1; also elsewhere on the board
GND: 3V3.1 (C), 5V0.1 (C), A1.2 (GND), B.1 (C), BMS.1 (C), BSPD.1 (C), B_HI.1 (C), B_MIS.1 (C), C.1 (C), C3.MINUS, C4.2, C5.2, C24.2, C27.2, C28.2, C61.2, C_HI.1 (C), C_MIS.1 (C), D.1 (C), D23.3 (A), D24.3 (A), E.1 (C), F.1 (C), G.1 (C), IMD.1 (C), SWOK.1 (C), U1.1 (GND), WDOG.1 (C); also elsewhere on the board
LATCH_BTN: LATCH.1 (C); also elsewhere on the board
unnamed: JP10.1, R142.2
unnamed: JP1.1, R47.2
unnamed: C61.1, R141.2, R142.1
unnamed: C24.1, R47.1, R52.2
unnamed: JP3.2, R52.1
unnamed: G.2 (A), R5.2
unnamed: LATCH.2 (A), R28.1
unnamed: B.2 (A), R20.2
unnamed: C.2 (A), R17.2
unnamed: D.2 (A), R14.2
unnamed: E.2 (A), R11.2
unnamed: F.2 (A), R8.2
unnamed: B_MIS.2 (A), R49.2
unnamed: C_HI.2 (A), R44.2
unnamed: C_MIS.2 (A), R48.2
unnamed: JP2.2, R141.1
unnamed: IMD.2 (A), R27.2
unnamed: BMS.2 (A), R26.2
unnamed: BSPD.2 (A), R25.2
unnamed: R24.2, WDOG.2 (A)
unnamed: 3V3.2 (A), R30.2
unnamed: R23.2, SWOK.2 (A)
unnamed: 5V0.2 (A), R29.2
unnamed: B_HI.2 (A), R41.2
OKHS_IN: R27.1; also elsewhere on the board
SHDN_B: R20.1; also elsewhere on the board
SHDN_C: R17.1; also elsewhere on the board
SHDN_D: R14.1; also elsewhere on the board
SHDN_E: R11.1; also elsewhere on the board
SHDN_F: R8.1; also elsewhere on the board
SHDN_G: R5.1; also elsewhere on the board
SOFTWARE_OK: R23.1; also elsewhere on the board
WATCHDOG_OK: R24.1; also elsewhere on the board

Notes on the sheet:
CAN_2 - Inverters CAN_3 - Sensors and anything else
Power Delivery
SHDN LEDS + Latch BTN
POWER/BSPD LEDS
CAN Termination Jumpers + TVS Protection

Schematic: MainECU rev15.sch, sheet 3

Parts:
C15, C16, C17, C18, C20, C57: CAPACITOR_0603_10V_0.1UF; 0603-CAP
C56: CAPACITOR_0603_10V_1UF; 0603-CAP
D21, D22: TVS__15V; SOT-23
JP9: DNP; 0603-RES
Q1: TRANSISTOR_N_MOS__DMG3406L-7; SOT-23
Q2: TRANSISTOR_P_MOS_SOT-23_DMP3056L-7; SOT-23
R33, R34, R62: RESISTOR_0603_10.2K; 0603-RES
R45, R51: RESISTOR_0603_43K; 0603-RES
R46, R50: RESISTOR_0603_1K; 0603-RES
R53: RESISTOR_0603_14K; 0603-RES
R54, R69, R133, R134, R147: RESISTOR_0603_10K; 0603-RES
R63, R64: RESISTOR_0603_1.13K; 0603-RES
R66: RESISTOR_0603_2.55K; 0603-RES
R68: RESISTOR_0603_2.18K; 0603-RES
R144, R146: RESISTOR_0603_5.1K; 0603-RES
TP3, TP4, TP6, TP7, TP8, TP9: TEST_POINT; 5015
U7: OPAMP_1_CHANNEL_OPA991; SC-70-5
U8, U9, U10, U11, U12: LOGICGATE_OR; SC-70-5
U13: LOGICGATE_NOR; SC-70-5
U15: LOGICGATE_AND_DCK3; SC-70-5
U24, U25, U26, U27: OPAMP_2_CHANNEL_OPA_2991; SOT-23-8
VR1, VR2: RESISTOR_TRIMPOT_10K_3362P; 3362P

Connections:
0V5: R62.2, R63.2, U25.5 (VIN+), U26.5 (VIN+)
0V26: R68.2, R69.2, U27.5 (VIN+)
2V65: R34.2, R66.2, U27.2 (VIN-)
4V5: R33.2, R64.2, U25.2 (VIN-), U26.2 (VIN-)
+3V3: R53.2, R66.1, R69.1, R134.2, VR1.3 (2); also elsewhere on the board
+5V: C15.1, C16.1, C17.1, C18.1, C20.1, R62.1, R64.1, U7.5 (VDD), U8.5 (VDD), U9.5 (VDD), U10.5 (VDD), U11.5 (VDD), U12.5 (VDD), U13.5 (VDD), U15.5 (VDD), U24.8 (VDD), U25.8 (VDD), U26.8 (VDD), U27.8 (VDD); also elsewhere on the board
+24V: D21.3 (C), Q2.2 (S), R146.2; also elsewhere on the board
BRAKE_1: U7.1 (VIN+), U27.3 (VIN+), U27.6 (VIN-); also elsewhere on the board
BRAKE_HIGH: U7.4 (VOUT), U15.1 (IN1); also elsewhere on the board
BRAKE_MISSING: U11.4 (OUT), U12.2 (IN2); also elsewhere on the board
BRAKE_OOR_HI: TP8.1, U11.2 (IN2), U27.1 (VOUT)
BRAKE_OOR_LO: TP9.1, U11.1 (IN1), U27.7 (VOUT)
BSPD_FAULT: U13.2 (IN2), U15.4 (OUT)
BSPD_OK: Q2.3 (D); also elsewhere on the board
BSPD_OK_LV: D22.3 (C), Q1.1 (G), R147.2, U13.4 (OUT)
CURRENT: R46.1, U25.3 (VIN+), U25.6 (VIN-); also elsewhere on the board
CURRENT_HIGH: U15.2 (IN2), U24.7 (VOUT); also elsewhere on the board
CURRENT_MISSING: U9.4 (OUT), U12.1 (IN1); also elsewhere on the board
CURRENT_OOR_HI: TP4.1, U8.1 (IN1), U25.1 (VOUT)
CURRENT_OOR_LO: TP7.1, U10.1 (IN1), U25.7 (VOUT)
GND: C15.2, C16.2, C17.2, C18.2, C20.2, C56.2, C57.2, D22.1 (A), Q1.2 (S), R33.1, R34.1, R45.2, R54.1, R63.1, R68.1, R133.1, R147.1, U7.2 (GND), U8.3 (GND), U9.3 (GND), U10.3 (GND), U11.3 (GND), U12.3 (GND), U13.3 (GND), U15.3 (GND), U24.4 (GND), U25.4 (GND), U26.4 (GND), U27.4 (GND), VR1.1; also elsewhere on the board
unnamed: R45.1, R46.2, U24.3 (VIN+)
unnamed: R134.1, VR2.3 (2)
unnamed: C56.1, C57.1, JP9.1, VR2.2 (3)
unnamed: R133.2, VR2.1
unnamed: R53.1, R54.2, U24.6 (VIN-)
unnamed: R50.2, R51.1, U24.2 (VIN-)
unnamed: R51.2, U24.1 (VOUT), U24.5 (VIN+)
unnamed: U7.3 (VIN-), VR1.2 (3)
unnamed: D21.1 (A), Q2.1 (G), R144.2, R146.1
unnamed: Q1.3 (D), R144.1
OOR_HI: U8.4 (OUT), U9.1 (IN1)
OOR_LO: U9.2 (IN2), U10.4 (OUT)
REFERENCE: JP9.2, R50.1, U26.3 (VIN+), U26.6 (VIN-); also elsewhere on the board
REFERENCE_OOR_HI: TP3.1, U8.2 (IN2), U26.1 (VOUT)
REFERENCE_OOR_LO: TP6.1, U10.2 (IN2), U26.7 (VOUT)
SIG_MISSING: U12.4 (OUT), U13.1 (IN1)

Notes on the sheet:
Current sensor is ISB-300-A-802 6.667mV/A ACU amp gain is 4.832x Decimation divider is 0.1103x Final current slope is 3.553mV/A 5kW at 530V is 9.434A Signal will be 33.522mV above reference Non-inverting op-amp with 1k and 41.2k has 42.2x gain. Boosts 5kW signal to 1.415V. Comparing to 1.375V refer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
BRAKE_1 needs to be positive coefficient signal (increasing brake request = inrcreasing voltage)
BRAKE_MISSING CALCULATIONS BRAKE_OOR_LO: 0.5 V * 0.6 = 0.30 .worst case input open circuit BRAKE_OOR_HI: 4.5V * .6 = 2.7 worst case input supply short circuit

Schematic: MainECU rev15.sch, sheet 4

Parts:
D3, D9, D10, D11, D12, D13, D14, D15, D16, D17: SCHOTTKY_SOD323_30V; SOD-323
D4, D5, D6, D7, D8: TVS_DO-214AA_30V; 1.5SMBJ
D19, D20: TVS__15V; SOT-23
K1, K2, K3, K4, K5: RELAY_DPDT_07DSMT; IM*G
Q3: TRANSISTOR_P_MOS_SOT-23_DMP3056L-7; SOT-23
Q4: TRANSISTOR_N_MOS__DMG3406L-7; SOT-23
R6, R9, R12, R15, R18, R21, R135, R136, R137: RESISTOR_0603_4.64K; 0603-RES
R7, R10, R13, R16, R19, R22, R138, R139, R140: RESISTOR_0603_36.5K; 0603-RES
R143, R149: RESISTOR_0603_10K; 0603-RES
R145, R148: RESISTOR_0603_5.1K; 0603-RES
S1: BUTTON; B3S-100X
U31: ADM8316WBX30; SOT-23-5
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

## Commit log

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2022-07-16 fixed isospi transformer
    [AMS Segment rev18.brd, AMS Segment rev18.sch]
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2022-08-03 Revert "renamed curr sensor temp net"
    This reverts commit 494a4ba0497bd697a3e918cf032b816e11a48ee2.
    [Accumulator Control Unit rev4.brd, Accumulator Control Unit rev4.sch]
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2022-08-07 fixed gain on differential op amps
    [Accumulator Control Unit rev4.brd, Accumulator Control Unit rev4.sch]
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2022-08-13 replaced transistors
    [MainECU rev11.sch]
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2022-09-17 connectors, filters, TCU CAN
    - added large 64 pin connectors for connector board and filter board
    - removed filters
    - added all CAN busses to TCU
    - added another ADC to main ECU
    [MainECU rev11.sch]
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2022-10-09 replaced ADIS16460 connector
    [MainECU rev11.sch]
2022-10-09 removed latch button. fixed interlock sense
    [MainECU rev11.sch]
2022-10-09 fixed imu pin
    [MainECU rev11.sch]
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2022-10-10 Update Discharge Board.sch
    Copied over necessary section of schematic from tsb-rev5 branch in Tractive System Boardrev5.sch
    [Discharge Board.sch]
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2022-10-13 Update Discharge Board.sch
    Added 1 Molex microfit right angle single row connector
    [Discharge Board.sch]
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2022-10-14 Correct sch->board
    [Discharge Board.brd, Discharge Board.sch]
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2022-10-14 Moved components around, tried to put connector as far away from TS and N$51 as possible
    [Discharge Board.brd]
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2022-10-14 corrected SHDN and GND wire width
    [Discharge Board.brd]
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2022-10-15 changes
    [12:05 AM] Lee, Zheng-Yin
    alright, I moved the names that were previously blocked by other things, added the dot, resized board(although I think I'll make another small adjustment), increased width of TS wires to 30 mil, and 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
    [Discharge Board.brd]
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2022-10-16 added missing files
    [AMS Enerdel Adapter rev7.brd, AMS Enerdel Adapter rev7.sch, AMS Enerdel Adapter rev8.brd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]
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2022-10-20 Replace B20 with B20-SHORTENED
    [Discharge Board.brd, Discharge Board.sch]
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2022-10-21 Revert "move parts to rough locations"
    This reverts commit c58f10de9c3e89850c49657a5bf15c62854b51d7.
    [Tractive System Board Rev5.brd, Tractive System Board Rev5.sch]
2022-10-21 Revert "merge conflicts"
    This reverts commit a6157c85e98bd56b769b7f19b8accda9bca1776f.
    [Tractive System Board Rev5.brd, Tractive System Board Rev5.sch]
2022-10-21 Revert "Revert "merge conflicts""
    This reverts commit 4e81cbec20ba5aa9c111a6f13ca01847208fa1cc.
    [Tractive System Board Rev5.brd, Tractive System Board Rev5.sch]
2022-10-21 Revert "Revert "move parts to rough locations""
    This reverts commit 152cedd13359bbd6401016ed664e67b9eb18d90e.
    [Tractive System Board Rev5.brd, Tractive System Board Rev5.sch]
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2022-10-23 Added 4 m3 mounting holes at correct distances away
    [Discharge Board.brd]
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2022-10-27 fixed dimensions
    [Accumulator Control Unit rev4.brd]
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2022-10-28 fixed wire stubs, DRC
    [MainECU rev11.brd]
2022-10-29 fixed BSPD
    [MainECU rev11.brd, MainECU rev11.sch]
2022-10-29 fixed exposed trace
    [MainECU rev11.brd]
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2022-10-30 fixed DRC
    [MainECU rev11.brd, MainECU rev11.sch]
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2022-10-31 fixed bent net in schematic
    [MainECU rev11.brd, MainECU rev11.sch]
2022-11-01 Drafted AMS Test Board
    Routed all 21 battery connectors on left side (no fuses).
    [AMS Test Board rev1.brd, AMS Test Board rev1.sch, BMS Test Board rev2.brd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]
2022-11-03 AMS Test Board Update
    Created additional space between battery connectors and added fuses.
    [AMS Test Board rev1.brd, AMS Test Board rev1.sch]
2022-11-03 Update Corner Board Rev1.sch
    Added MAX6176 part to Corner Board Rev1 schematic.
    [Corner Board Rev1.sch]
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2022-11-13 Added new pin assignments for buttons, leds, and diall
    Still need to add read circuitry for dial!
    [Dashboard rev6.sch]
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2022-11-17 swapped resistors on "signal missing" comparators
    [MainECU rev11.brd, MainECU rev11.sch]
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2022-11-20 Revert "Added new pin assignments for buttons, leds, and diall"
    This reverts commit a6f22fc0d68318eb39298f9c1ce3419cd5d91f64.
    Revert "Began adding LEDs"
    This reverts commit 7e994de39b0e8e84318d6bff5e1ce333b0dba15a.
    [Dashboard rev6.brd, Dashboard rev6.sch]
2022-11-20 Revert "Revert "Added new pin assignments for buttons, leds, and diall""
    This reverts commit 56de9ed2ceca7c35ee8ee5d09982bb1f6325394b.
    [Dashboard rev6.brd, Dashboard rev6.sch]
2022-11-20 Dash Changes (Should not be here)
    Revert "Added new pin assignments for buttons, leds, and diall"
    Revert "Revert "Added new pin assignments for buttons, leds, and diall""
    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
    [Dashboard rev6.brd, Dashboard rev6.sch]
2022-11-20 Revert "Dash Changes (Should not be here)"
    This reverts commit 6c5b3a284606ee9165e31102d50f5ac554dd5126.
    [Dashboard rev6.brd, Dashboard rev6.sch]
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2022-11-21 Replaced CAN circuitry, changed shutdown resistance dividers, added labels
    [Dashboard rev6.brd, Dashboard rev6.sch]
2022-11-21 Fixed labeling and frame info
    [Dashboard rev6.sch]
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2022-11-29 replaced 5-pin connector with new right angle
    [Discharge Board rev2.brd, Discharge Board rev2.sch]
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2022-12-02 corrected via placement, move TS+,- away from each other, switched up orientation of 2 resistors
    [Discharge Board rev2.brd]
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2022-12-02 fixed 1 airwire
    [Discharge Board rev2.brd]
2022-12-02 fixed another airwire
    [Discharge Board rev2.brd]
2022-12-02 fixed wire stubs
    [Discharge Board rev2.brd]
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2022-12-04 fixed trace width
    [EMI Shielding Test.brd]
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2022-12-05 AMS Test Board Rev2 LTC6820 and Transformer Schematic
    Recreated the schematic of the Teensy 4.0, LTC6820, and transformer from the Accumulator Control Unit.
    [AMS Test Board rev1.brd, AMS Test Board rev1.sch]
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2022-12-05 AMS Test Board Rev2
    Placed components onto the board in a general layout and started routing.
    [AMS Test Board rev1.brd]
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2022-12-06 Update AMS Test Board rev1.brd
    Drafted a possible routing design for the right ACU sector of the board.
    [AMS Test Board rev1.brd]
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2022-12-09 fixed spacing, changed connectors
    [EMI Shielding Test.brd, EMI Shielding Test.sch]
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2022-12-15 everything except fixing dxf
    [Tractive System Board Rev5.brd]
2022-12-15 small fix
    [Tractive System Board Rev5.brd]
2022-12-15 fixed outline
    [Tractive System Board Rev5.brd]
2022-12-15 minor schematic fixes
    [Tractive System Board Rev5.brd, Tractive System Board Rev5.sch]
2022-12-15 unrouted broken
    [Accumulator Control Unit rev4.brd]
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2022-12-19 fixed everything except fuse
    [Tractive System Board Rev5.brd, Tractive System Board Rev5.sch]
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2022-12-20 Update AMS Test Board rev1.brd
    Created a GND polygon on the bottom layer to connect all the GND for easier routing on the top layer.
    [AMS Test Board rev1.brd]
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2022-12-20 Revert "attempted replacing 1 relay"
    This reverts commit 32283372b2d5891ba4c134fe29f47b6de259f84f.
    [Charger Control Board rev8.brd, Charger Control Board rev8.sch]
2022-12-20 Replaced K1,K2,K3, relays
    [Charger Control Board rev8.sch]
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2022-12-21 Update AMS Test Board rev1.brd
    Drafted a routing for the right side of the board. There's still two wires that are too close to each other.
    [AMS Test Board rev1.brd]
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2022-12-21 fixed BSPD. removed 2 transceivers. routing.
    [MainECU rev12.brd, MainECU rev12.sch]
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2022-12-21 fixed inconsistencies
    [Charger Control Board rev8.brd, Charger Control Board rev8.sch]
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2022-12-21 replace 12V symbol as well as C7 in 5V regulator
    [Charger Control Board rev8.sch]
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2022-12-21 Revert "replace 12V symbol as well as C7 in 5V regulator"
    This reverts commit 6aab972d1cefc5b4b389110758fdc5635f8030d3.
    [Charger Control Board rev8.sch]
2022-12-21 Revert "changed ext power in"
    This reverts commit f53486e2ac9dfbd128d81dc2483ca451050466bb.
    [Charger Control Board rev8.brd, Charger Control Board rev8.sch]
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2022-12-22 replaced with TCAN1051 CAN transceiver
    [Charger Control Board rev8.brd, Charger Control Board rev8.sch]
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2022-12-22 replaced R3,R4,R5,R6 resistors
    [Charger Control Board rev8.brd, Charger Control Board rev8.sch]
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2022-12-22 fixed silkscreen, polyfill
    [MainECU rev12.brd]
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2022-12-22 Resolved merge conflicts
    [Dashboard rev6.sch]
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2022-12-23 tiny silkscreen fix
    [MainECU rev12.brd]
2022-12-24 replaced fuse in schematic
    [Tractive System Board Rev5.brd, Tractive System Board Rev5.sch]
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2022-12-24 added 122 fuse holder, fixed routing
    [Tractive System Board Rev5.brd, Tractive System Board Rev5.sch]
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2022-12-27 removed 46/57 airwire errors
    [Charger Control Board rev8.brd]
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2022-12-27 fixed nets. added bulk capacitance
    [EMI Shielding Test.brd, EMI Shielding Test.sch]
2022-12-28 cleared up some small errors
    [Charger Control Board rev8.brd]
2022-12-28 small errors
    [Charger Control Board rev8.brd]
2022-12-28 fixed DRC errors
    [Charger Control Board rev8.brd]
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2022-12-28 fixed up some texts
    [Charger Control Board rev8.brd]
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2022-12-31 swapped pull downs, changed tstop
    [Corner Board Rev2.brd, Corner Board Rev2.sch]
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2023-01-01 fixed silkscreen
    [Connector Board rev1.brd]
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2023-01-03 updated from latest library. did not change 180uF cap.
    board was ordered with erroneous footprint for C3. This should be fixed for next rev.
    [Tractive System Board Rev5.brd, Tractive System Board Rev5.sch]
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2023-01-16 Replaced the old capacitor with updated, bigger capacitor and rearranged routing slightly
    [Tractive System Board Rev6.brd, Tractive System Board Rev6.sch]
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2023-01-22 added wire lengths, missing discharge HV wire lengths
    [Accumulator TS Schematic.sch, Tractive System Schematic.sch]
2023-01-22 changed BSPD, fixed precharger vdd
    [Accumulator TS Schematic.sch, BSPD System Schematic.sch, Shutdown Circuit Schematic.sch]
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2023-01-23 Corner Board Rev3 Unfinished
    Rerouted components to decrease board size. Work still needed.
    [Corner Board Rev3.brd, Corner Board Rev3.sch]
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2023-01-25 updated from latest library. fixed CAN1
    [MainECU rev13.brd, MainECU rev13.sch]
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2023-01-25 FINISHED Corner Board Rev3
    Fixed minor mistakes.
    [Corner Board Rev3.brd]
2023-01-25 ams-text-board-rev3
    Grounded the LTC6820 in rev2 error
    [AMS Test Board rev3.brd, AMS Test Board rev3.sch]
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2023-02-03 Fixed pullups and voltage regulator
    [Corner Board Rev3.brd, Corner Board Rev3.sch]
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2023-02-03 fixed board text
    [MainECU rev13.brd]
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2023-02-24 replace w/ tuned resistor
    [Accumulator Control Unit rev5.brd, Accumulator Control Unit rev5.sch]
2023-02-24 replace wires w 10mil
    [Accumulator Control Unit rev5.brd]
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2023-04-21 tsb-update
    Replaced 24-to-5V linear regulator to DC-DC converter
    [Tractive System Board Rev6.brd, Tractive System Board Rev6.sch]
2023-04-21 Resistor Update
    Changed the wattage of the 3.3k ohm resistor from 0.2W to 0.3W
    [Tractive System Board Rev6.brd, Tractive System Board Rev6.sch]
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2023-07-18 EN/UVLO TS divider
    Added a resistor divider from TS+FUSED to enable the LT8613 Flyback Controller and turn on AIL when TS+FUSED >60V.
    [Tractive System Board Rev7.sch]
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2023-07-21 Replaced J1 & J2 connector with correct MPN and standardized all HV nets to 0.024" width
    [Tractive System Board Rev7.brd, Tractive System Board Rev7.sch]
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2023-07-21 tsb-rev7 update
    Added DNP resistor in parallel to R30 of the input to the optoisolator incase R30 is not enough.
    [Tractive System Board Rev7.brd, Tractive System Board Rev7.sch]
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2023-07-27 tsb-rev7 update
    Updated voltage divider and added bypass capacitors to EN/UVLO pin on the flyback controller
    [Tractive System Board Rev7.brd, Tractive System Board Rev7.sch]
2023-07-27 tsb-rev7 update
    Removed 1uF bypass capacitor to EN/UVLO input of flyback controller
    [Tractive System Board Rev7.brd, Tractive System Board Rev7.sch]
2023-07-28 tsb-rev7 update
    Get rid of R15 & R18 (Didn't account for Thevenin resistance of the resistor divider)
    [Tractive System Board Rev7.brd, Tractive System Board Rev7.sch]
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2023-08-20 tsb-rev7-schematic-update
    Updated some capacitors in the LT8315 buck converter topology to be higher rated
    [Tractive System Board Rev7.brd, Tractive System Board Rev7.sch]
2023-08-20 tsb-rev7-schematic-update
    Added HV Rdcm and higher rated output filter capacitor on the LT8315 buck converter topology
    [Tractive System Board Rev7.brd, Tractive System Board Rev7.sch]
2023-08-21 tsb-rev7-schematic-review
    Self-reviewed sheet 1 of tsb-rev7 schematic, noticing that some HV nets were not legitimately connected
    [Tractive System Board Rev7.brd, Tractive System Board Rev7.sch]
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2023-08-28 tsb-rev8 update
    fixed net bugs
    [Tractive System Board Rev8.brd, Tractive System Board Rev8.sch]
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2023-09-24 Revert "remove shayan filter"
    This reverts commit e50d2a7a265c93c6b2150033f3e34a844e27dda6.
    [Corner Board Rev4.brd, Corner Board Rev4.sch]
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2023-09-25 eagle crashed but prelim routing complete
    fix signal integrity on digital signals
    [Corner Board Rev4.brd, Corner Board Rev4.sch]
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2023-09-27 fixed voltage divider gain text
    [Corner Board Rev4.sch]
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2023-09-29 tsb-rev8-layout-update
    rearrange entire board, including swapping ts+ & ts- connectors and shrinking
    [Tractive System Board Rev8.brd]
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2023-09-29 tsb-rev8-layout-update
    trace-length matched IT+- and IP+-. Took me AN HOUR AND HALF
    [Tractive System Board Rev8.brd]
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2023-09-30 tsb-rev8-schematic-update
    Added, DNP resistor for connecting EN/UVLO to INTVCC in the case that we don't want to use selective 60V chip activation
    [Tractive System Board Rev8.brd, Tractive System Board Rev8.sch]
2023-09-30 tsb-rev8-layout-update
    Fixed net issue to CAP 55. Finetuned buck parts placement, started initial routing
    [Tractive System Board Rev8.brd, Tractive System Board Rev8.sch]
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2023-09-30 tsb-rev8-layout-update
    updated amc3330 routing with no NC and parts placement of en/uvlo resistor network. reconsidering placement of ts- fuse and connector
    [Tractive System Board Rev8.brd, Tractive System Board Rev8.sch]
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2023-09-30 ACU Rev 6 save
    Did some routing and removed 1 transformer also moved teensy pins
    [Accumulator Control Unit rev6.brd, Accumulator Control Unit rev6.sch]
2023-10-01 Fixed 7404 capacitor value
    [Sensor Acquisition Board Rev5.sch]
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2023-10-01 merged can lines, changed brake missing, added 12vdcdc
    [MainECU rev15.brd, MainECU rev15.sch]
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2023-10-04 tsb-rev8-layout-update
    replaced m3 mounting holes for m4s
    [Tractive System Board Rev8.brd]
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2023-10-07 Added CAN and RS485 bidirectional TVS/ESD protection
    Telemetry CAN might not terminate on SAB, make sure to remove termination resistors if not.
    Still need to add other protocol protection circuits, TVS, Zener, Shottky, etc. Reverse polarity protection.
    Power LEDs and test points.
    Thermistor math.
    [Sensor Acquisition Board Rev5.sch]
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2023-10-08 tsb-rev8-layout-update
    Finished buck converter routing. Routed TS-FUSED to iso amps and buck. Placed TPs. Readjusted all via drill sizes to match hv pcb width
    [Tractive System Board Rev8.brd]
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2023-10-11 tsb-rev8-layout-update
    added via clearance of non PGND vias for the PGND polygon pour
    [Tractive System Board Rev8.brd]
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2023-10-13 Cleared DRC errors
    Cleared DRC errors
    [AMS Segment rev19.brd]
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2023-10-15 DRC fix for sunstone
    changed vias for decreasing the errors
    [AMS Segment rev19.brd]
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2023-10-16 tsb-rev8-layout-update
    rerouted buck converter topology to shorten input-capacitor, diode, and source-node hot loop
    [Tractive System Board Rev8.brd]
2023-10-16 tsb-rev8-layout-update
    solves DRC errors
    [Tractive System Board Rev8.brd]
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2023-10-17 Aero CAN swap straight for right angle 4-pin molex
    [Sensor Acquisition Board Rev5.sch]
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2023-10-21 fixed transformer spacing
    [Corner Board Rev4.brd]
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2023-10-22 Adjusted schematic
    SAB and corner board shutdown connection
    Spare CAN supply rail jumpers
    Get rid of 10V reference
    Adjusted thermistor resistors and filter
    Swapped RS232 and RS485 chip
    Switch to Teensy 4.0
    [Sensor Acquisition Board Rev5.sch]
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2023-10-23 Adjusted schematic
    Swapped LTC1563 for HyTechDevices
    [SAB Test Board rev 1.sch]
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2023-10-23 Swapped MCP2515 2551 for HyTechDevices
    [SAB Test Board rev 1.sch]
2023-10-23 tsb-rev8-layout-udpate
    fixed DRC errors
    [Tractive System Board Rev8.brd]
2023-10-23 tsb-rev8-layout-update
    some quick fixes
    [Tractive System Board Rev8.brd]
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2023-10-23 replaced single opa's with dual package
    [MainECU rev15.brd, MainECU rev15.sch]
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2023-10-24 tsb-rev8-layout-update
    some fixes. reviewed with team
    [Tractive System Board Rev8.brd]
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2023-10-26 Revert "Update Accumulator Control Unit rev6.brd"
    This reverts commit 9c4b5f8b499e9f513b432cb31a22ac7dede785b9.
    [Accumulator Control Unit rev6.brd]
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2023-10-26 replaced diode
    [SAB Test Board rev 1.brd, SAB Test Board rev 1.sch]
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2023-10-27 Swap for 14V TVS
    [Sensor Acquisition Board Rev5.sch]
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2023-10-30 Fixed Shayan's bad work
    [keychain_rev4.brd]
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2023-10-30 Connected RX correctly
    [SAB Test Board rev 1.brd, SAB Test Board rev 1.sch]
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2023-10-30 DRC fix
    [SAB Test Board rev 1.brd]
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2023-10-31 Replaced iso_TS and iso_Pack processing resistors
    [Accumulator Control Unit rev6.brd, Accumulator Control Unit rev6.sch]
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2023-11-01 approved all correct overlaps
    [MainECU rev15.brd]
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2023-11-05 Revert "Create Shutdown Circuit Schematic.sch"
    This reverts commit d8c95aed7c5d215abf73d8820e7a9181000d854e.
    [Shutdown Circuit Schematic.sch]
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2023-11-06 some routes before Eagle crashes
    [Sensor Acquisition Board Rev5.brd, Sensor Acquisition Board Rev5.sch]
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2023-11-07 fixing stuff from brd review
    [MainECU rev15.brd, MainECU rev15.sch]
2023-11-07 major routing fixes
    [MainECU rev15.brd]
2023-11-07 quick fix
    [MainECU rev15.brd]
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2023-11-13 fixing broken stuff
    [Accumulator TS Schematic.sch, BSPD System Schematic.sch, Shutdown Circuit Schematic.sch]
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2023-11-18 Fixes to power planes and routing
    [Dashboard rev7.brd, Dashboard rev7.sch]
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2023-11-19 Cosmetic fixes
    [Dashboard rev7.brd]
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2023-11-25 Finishing up
    Swap connectors
    Round corners
    Edge plating
    [Sensor Acquisition Board Rev5.brd, Sensor Acquisition Board Rev5.sch]
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2023-11-27 no drc errors
    [Corner Board Rev4.brd]
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2023-11-28 some route fix
    [Sensor Acquisition Board Rev5.brd]
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2023-12-02 fixing dif pairs spaciong
    [MainECU rev15.brd, MainECU rev15.sch]
2023-12-02 fixed diff pair routing
    [MainECU rev15.brd, MainECU rev15.sch]
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2023-12-02 swaped some of the pins around for easier routing
    [Accumulator Control Unit rev6.brd, Accumulator Control Unit rev6.sch]
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2023-12-02 no more DRC errors
    [Accumulator Control Unit rev6.brd]
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2023-12-03 fixed merge conflict
    [MainECU rev15.brd]
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2023-12-04 some routing fixed will do the rest once I get back
    [Accumulator Control Unit rev6.brd]
2023-12-04 fixed all drc errrors again
    [Accumulator Control Unit rev6.brd]
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2023-12-04 acu-rev6-update
    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
    [Accumulator Control Unit rev6.brd, Accumulator Control Unit rev6.sch]
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2023-12-05 fixed conflicts
    [Connector Board rev2.brd]
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2023-12-05 swap max's for 1uF cap
    [Sensor Acquisition Board Rev5.brd, Sensor Acquisition Board Rev5.sch]
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2023-12-10 connector board fixes
    [Connector Board rev2.brd, Connector Board rev2.sch]
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2023-12-19 swapped rs232 and rs485 caps for higher voltage ratings
    [Sensor Acquisition Board Rev5.brd, Sensor Acquisition Board Rev5.sch]
2023-12-19 updates on things that are wrong
    [Shutdown Circuit Schematic.sch]
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2023-12-20 DRC and via Fixes
    [Sensor Acquisition Board Rev5.brd]
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2023-12-25 Revert "rs485 firmware pin notes"
    This reverts commit 5b99e37346135fe8be61798346ccc42894d34ddc.
    [Sensor Acquisition Board Rev5.sch]
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2023-12-29 swapped 20 pin molex and adjusted connector pos
    [Connector Board rev2.brd, Connector Board rev2.sch]
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
